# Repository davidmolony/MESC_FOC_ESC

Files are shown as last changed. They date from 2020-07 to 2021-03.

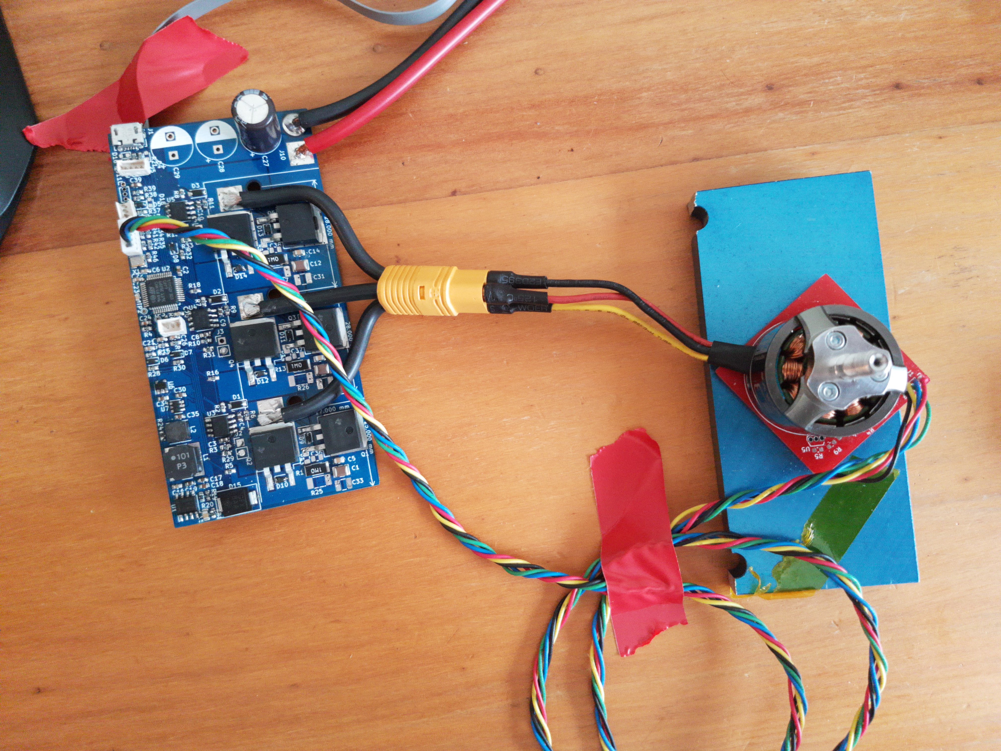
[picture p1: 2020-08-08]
MESC First Build and Propdrive 2826-1200kV.jpg

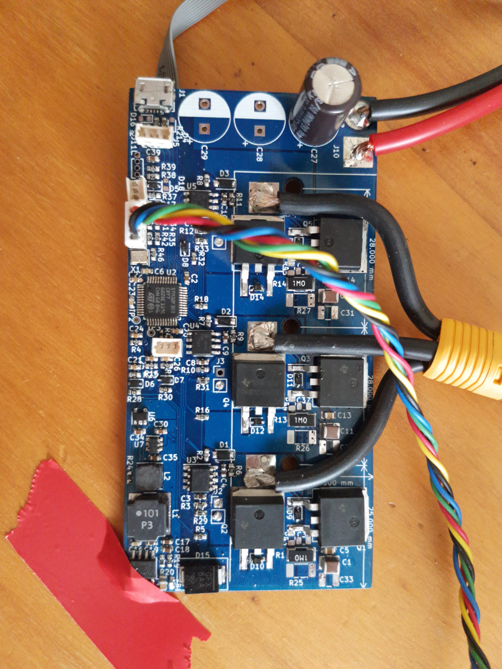
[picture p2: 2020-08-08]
MESC First build.jpg

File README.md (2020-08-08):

# MESC_FOC_ESC
MESC, Molony ESC, STM32F303 based FOC+BLDC ready, HALL, Encoder, Sensorless, single sides, 2 layer, ~90A @48V

This ESC is intended as a cost optimised alternative to the VESC, by utilising:

Standalone, industry standard footprint gate drivers

Standard D2PAK or H2PAK FETs

Cheap (~2.5$) STM32F303CB microcontroller

Board dimensions 100mmx50mm, so that it can be panelised and manufactured by JLCPCB, or two boards can be combined into one 100mm2 JLCPCB

It is not cross compatible with VESC software, and does not intend to be. VESC has run away with itself in terms of cost, firmware abstraction... in the opinion of this project's author.

# Current Status:  
First build has been made. All functions... function.
Photos in folder! Video of prelim run to be added to Youtube.
Step down works
Step up for Gate drives works
Chip works, all inputs and outputs works
Some concerns about stability of internal opamps... Returning 1.5V instead of 1.6V. First chip soldered returned 1V, and fluctuated by +0.3/-0.1V. 
Motor spins in BLDC mode (6 step) with hall sensors, on Propdrive 2826 1200kV and with APS8072 50kV. Current run up to 20A phase, with minimal PCB heating with no heatsink. Only run to 23V so far, owing to PSU limitation.
FET switching time rather slow with 5 ohm resistors, limiting peak current to 2A (not counting FET and Gate drive resistance) will reduce to 2R7.

# Layout:  
Layout optimised to minimise current loop path, and keep the board completely single sided assembly.

For thermal management, the FETs have vias underneath the drains, which can be interfaced with a heatsink on the PCB underside, using silicone pad/thermal paste & insulator.

# MCU uses:
Timer1 on PA8,9,10 (high) and PB13,14,15 for PWM generation.

Onboard opamps for current sensing and paralelled comparators input on pins PA1,7, PB0.

Phase voltages can be measured on PA3,4,5, or alternatively, digitally read to detect ZC .

Main voltage can be read on PA0.

# Interfaces:
External Interfaces include Hall/Encoder, I2C, PWM in, UART, USB FS.

Hall sensors on Timer4 PB6,7,8, alternatively Encoder can be run on Tim4 PB6,7

Timer3 channel 1 for standard RC PWM input.

USART3 Tx Rx on PB10,11.
USB on PA11,12, with 1k5 pullup to signal FS mode. Canbe used for reflashing (hypothetically).

I2C1 on PA15(SCL) and PB9(SDA), with a plug for a standard SSD1306 breakout. Alternatively, inertial sensor board could be plugged on breakout wire.

Expected BoM cost:  
0.4USD board  
6x2USD FETs  
2.5USD MCU  
3x1USD gate drives  
1USD SMPS converter  
0.4USD inductor  
??? connector cost (dependent on what's fitted, wire in...)  
0.3USD linear reg  
~3USD caps (dependent on how many you want to solder on, which is dependent on distance to battery, desire to comply with EMC, headroom above FET voltage... etc.)  
0.6USD shunts and other resistors  
0.3USD Optional TVS diode, primarily to protect SMPS, which is only rated to 65V  
Total: ~23-24USD

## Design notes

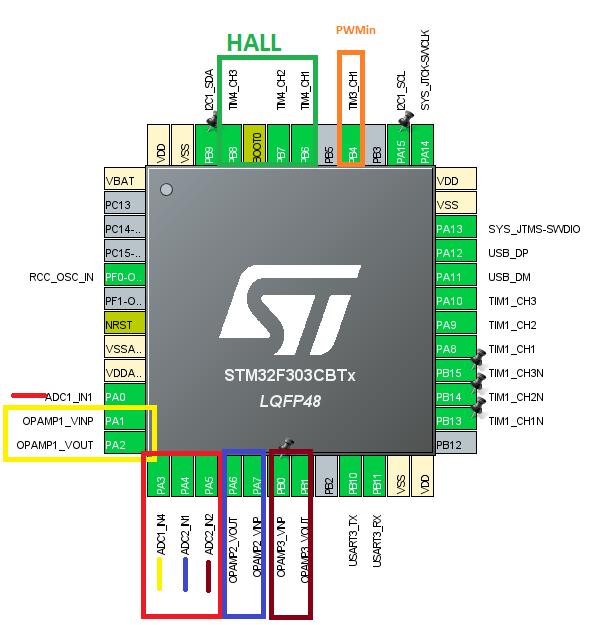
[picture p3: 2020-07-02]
CubeMX Pinout Annotated.JPG

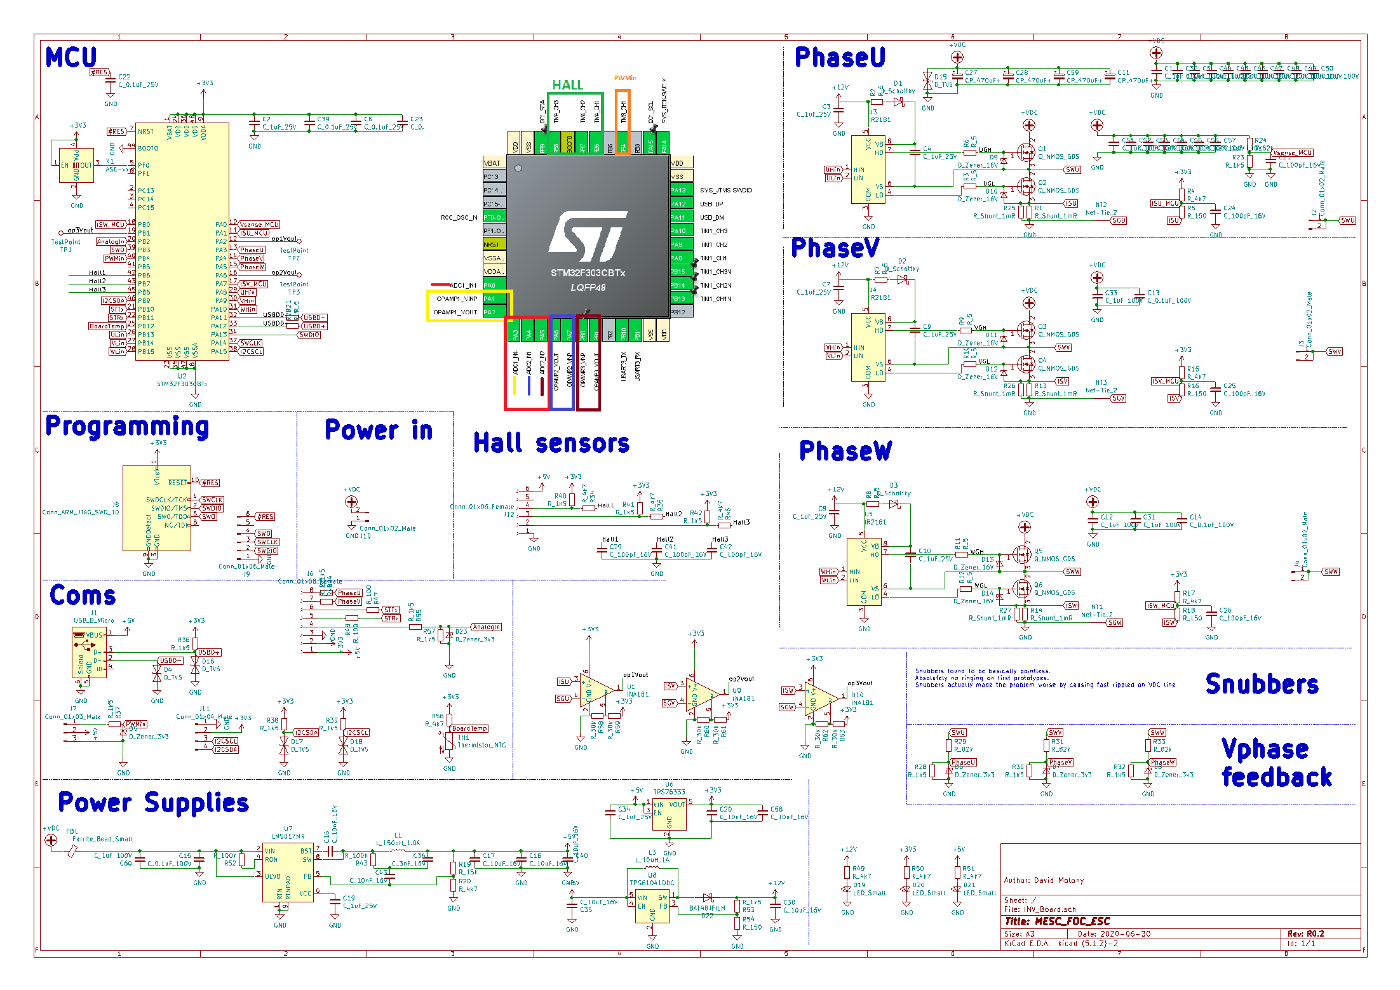
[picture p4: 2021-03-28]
Schematic MESC_FOC.png

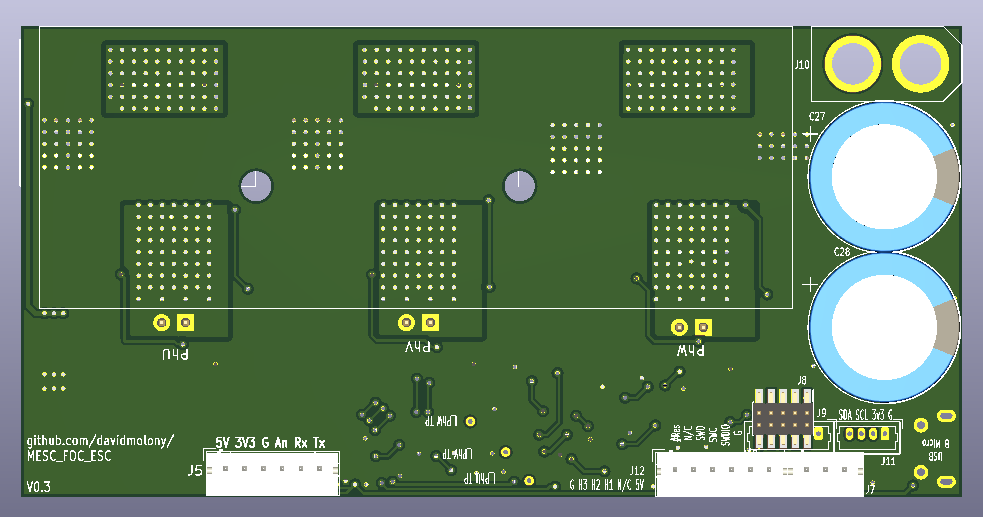
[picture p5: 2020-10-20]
MESC_FOC_ESC_Bottom_View.png

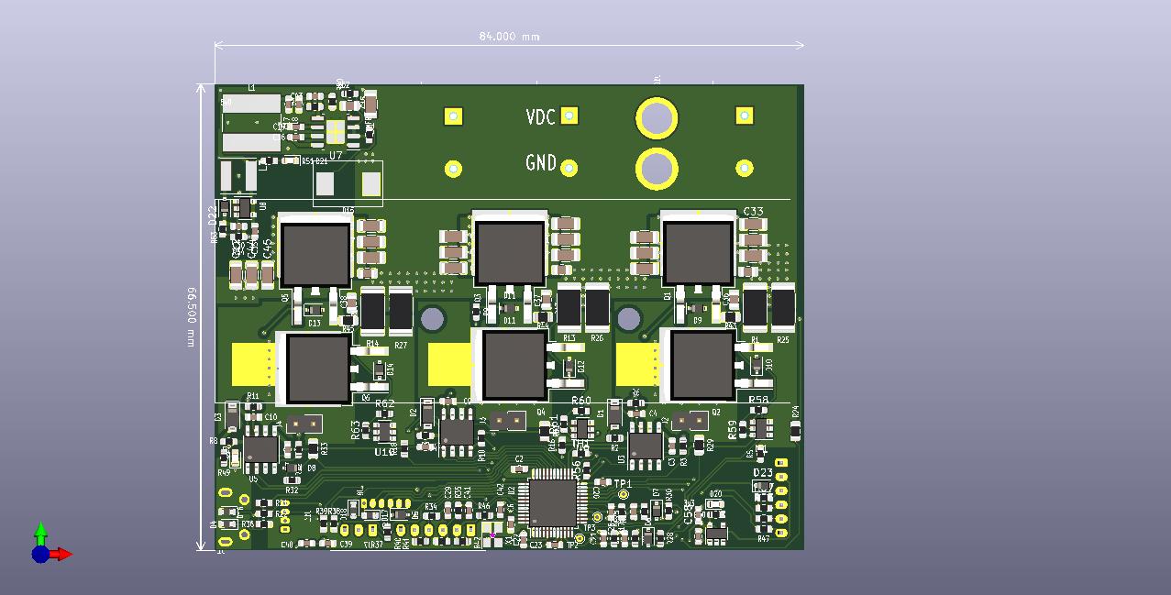
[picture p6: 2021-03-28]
V0.4 board top.jpg

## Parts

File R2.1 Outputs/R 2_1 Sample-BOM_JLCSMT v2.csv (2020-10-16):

Comment | Designator | Footprint | LCSC Part #(optional)
10uF 16V | C17,C18,C20,C30,C40 | 0603_C | C19702
1uF 25V | C2,C3,C4,C7,C8,C9,C10,C16,C19,C34 | 0603_C | C15849
100pF 16V | C21,C24,C25,C26,C29,C41,C42 | 0603_C | C14858
0.1uF 25V | C6,C22,C23,C35,C39 | 0603_C | C14663
0.01uF 100V | C36,C37,C38 | 0805_C | C22423
Zener 16V | D9,D10,D11,D12,D13,D14 | SOD-323_D | C150089
0603 LED | D19,D20,D21 | 0603_D | C2286
Schottky diode | D22 | SOD-323F_D | C2128
Schottky | D1,D2,D3 | SOD-123FL_D | C64898
Zener_3v3 | D5,D6,D7,D8 | SOD-323_D | C145245
MOSFET | Q1,Q2,Q3,Q4,Q5,Q6 | TO263-2_Q | C410926
150? | R5,R16,R18,R54 | 0603_R | C22808
15k? | R19 | 0603_R | C22809
4k7? | R4,R15,R17,R20,R34,R35,R46,R49,R50,R51 | 0603_R | C23162
5? | R2,R3,R6,R7,R8,R9,R10,R11,R12,R21,R22 | 0603_R | C23164
82k? | R24,R29,R31,R33 | 0805_R | C17840
2M? | R1,R13,R14,R25,R26,R27 | 2512_R | C60923
1k5? | R23,R28,R30,R32,R36,R37,R38,R39,R40,R41,R42,R53 | 0603_R | C22843
1? | R43,R44,R45 | 0805_R | C25271
100? | R47,R48 | 0603_R | C22775
30k? | R52 | 0603_R | C22984
STM32F303CB | U2 | LQFP-48_7.0x7.0x0.5P | C108516
TPS76333 | U6 | SOT-323-5_U | C110463
TPS61041DDC | U8 | SOT-323-5_U | C7722
OSCILLATORS 8MHz | X1 | SMD-OSC-3225_4P | C70556

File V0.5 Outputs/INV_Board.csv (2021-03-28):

Comment | Designator | Footprint | LCSC
C_1uF 100V | C1,C12,C31,C32,C33,C44,C45,C46,C47,C48,C49,C50,C51,C52,C53,C54,C55,C56,C57,C60 | Capacitor_SMD:C_1206_3216Metric | C13832
C_10nF_16V | C16,C43 | Capacitor_SMD:C_0603_1608Metric | C57112
C_10uF_16V | C17,C18,C20,C30,C35,C40,C58 | Capacitor_SMD:C_0603_1608Metric | C19702
C_1uF_25V | C2,C3,C4,C7,C8,C9,C10,C19,C34 | Capacitor_SMD:C_0603_1608Metric | C15849
C_100pF_16V | C21,C24,C25,C26,C29,C41,C42 | Capacitor_SMD:C_0603_1608Metric | C14858
C_0.1uF_25V | C6,C22,C23,C39 | Capacitor_SMD:C_0603_1608Metric | C14663
CP_470uF+ | C11,C27,C28,C59 | Capacitor_THT:CP_Radial_D16.0mm_P7.50mm
C_3nF_16V | C36 | Capacitor_SMD:C_0603_1608Metric | C1613
C_0.1uF_100V | C5,C13,C14,C15 | Capacitor_SMD:C_0805_2012Metric | C28233
D_Zener_16V | D9,D10,D11,D12,D13,D14 | Diode_SMD:D_SOD-323 | C150089
D_TVS | D15 | INV_Board:DO-214AB
D_TVS | D4,D16,D17,D18 | Diode_SMD:D_0603_1608Metric
LED_Small | D19,D20,D21 | LED_SMD:LED_0603_1608Metric | C2286
BAT48JFILM | D22 | Diode_SMD:D_SOD-323 | C2128
D_Schottky | D1,D2,D3 | Diode_SMD:D_SOD-123 | C64898
D_Zener_3v3 | D5,D6,D7,D8,D23 | Diode_SMD:D_SOD-323 | C145245
Ferrite_Bead_Small | FB1 | Resistor_SMD:R_0603_1608Metric | BLM18KG121TN1D
USB_B_Micro | J1 | Connector_USB:USB_Micro-B_Molex-105017-0001
Conn_01x02_Male | J10 | INV_Board:XT60
Conn_01x04_Male | J11 | Connector_Molex:Molex_PicoBlade_53047-0410_1x04_P1.25mm_Vertical
Conn_01x06_Female | J12 | Connector_JST:JST_PH_B6B-PH-K_1x06_P2.00mm_Vertical
Conn_01x02_Male | J2,J3,J4 | Connector_Wire:SolderWirePad_1x02_P5.08mm_Drill1.5mm
Conn_01x08_Female | J6 | Connector_JST:JST_PH_B8B-PH-K_1x08_P2.00mm_Vertical
Conn_01x03_Male | J7 | Connector_JST:JST_PH_B3B-PH-K_1x03_P2.00mm_Vertical
Conn_ARM_JTAG_SWD_10 | J8 | Connector_PinHeader_1.27mm:PinHeader_2x05_P1.27mm_Vertical_SMD
Conn_01x06_Male | J9 | Connector_Molex:Molex_PicoBlade_53047-0610_1x06_P1.25mm_Vertical
L_150uH_1.0A | L1 | Inductor_SMD:L_Bourns-SRN8040_8x8.15mm | C340248
L_10uH_1A | L3 | Inductor_SMD:L_Taiyo-Yuden_NR-50xx | C408339
Net-Tie_2 | NT1,NT2,NT3 | NetTie:NetTie-2_SMD_Pad0.5mm
Q_NMOS_GDS | Q1,Q2,Q3,Q4,Q5,Q6 | Package_TO_SOT_SMD:TO-263-2 | C455308
IPT015N10N5 | Q7,Q8,Q9,Q10,Q11,Q12 | Package_TO_SOT_SMD:Infineon_PG-HSOF-8-1 | C108964
R_150 | R5,R16,R18,R54 | Resistor_SMD:R_0603_1608Metric | C22808
R_15k | R19 | Resistor_SMD:R_0603_1608Metric | C22809
R_4k7 | R4,R15,R17,R20,R34,R35,R46,R49,R50,R51,R56 | Resistor_SMD:R_0603_1608Metric | C23162
R_5 | R2,R3,R6,R7,R8,R9,R10,R11,R12,R21,R22 | Resistor_SMD:R_0603_1608Metric | C23164
R_82k | R24,R29,R31,R33 | Resistor_SMD:R_0805_2012Metric | C17840
R_Shunt_1mR | R1,R13,R14,R25,R26,R27 | Resistor_SMD:R_2512_6332Metric | C270947
R_1k5 | R23,R28,R30,R32,R36,R37,R38,R39,R40,R41,R42,R44,R45,R53,R55,R57 | Resistor_SMD:R_0603_1608Metric | C22843
R_100 | R47,R48 | Resistor_SMD:R_0603_1608Metric | C22775
R_100k | R43,R52 | Resistor_SMD:R_0603_1608Metric | C25803
R_30k | R58,R59,R60,R61,R62,R63 | Resistor_SMD:R_0603_1608Metric | C22984
Thermistor_NTC | TH1 | Resistor_SMD:R_0603_1608Metric | C92367
TestPoint | TP1,TP2,TP3 | TestPoint:TestPoint_THTPad_D1.0mm_Drill0.5mm
INA181 | U1,U9,U10 | Package_TO_SOT_SMD:SOT-23-6
STM32F303CBTx | U2 | Package_QFP:LQFP-48_7x7mm_P0.5mm | C108516
IR2181 | U3,U4,U5 | Package_SO:SOIC-8_3.9x4.9mm_P1.27mm | C380794
TPS76333 | U6 | Package_TO_SOT_SMD:SOT-23-5 | C150720
LM5017MR | U7 | Package_SO:SOIC-8-1EP_3.9x4.9mm_P1.27mm_EP2.95x4.9mm_Mask2.71x3.4mm_ThermalVias | C34355
TPS61041DDC | U8 | Package_TO_SOT_SMD:SOT-23-5 | C7722
ASE-xxxMHz | X1 | Oscillator:Oscillator_SMD_Abracon_ASE-4Pin_3.2x2.5mm | C70556

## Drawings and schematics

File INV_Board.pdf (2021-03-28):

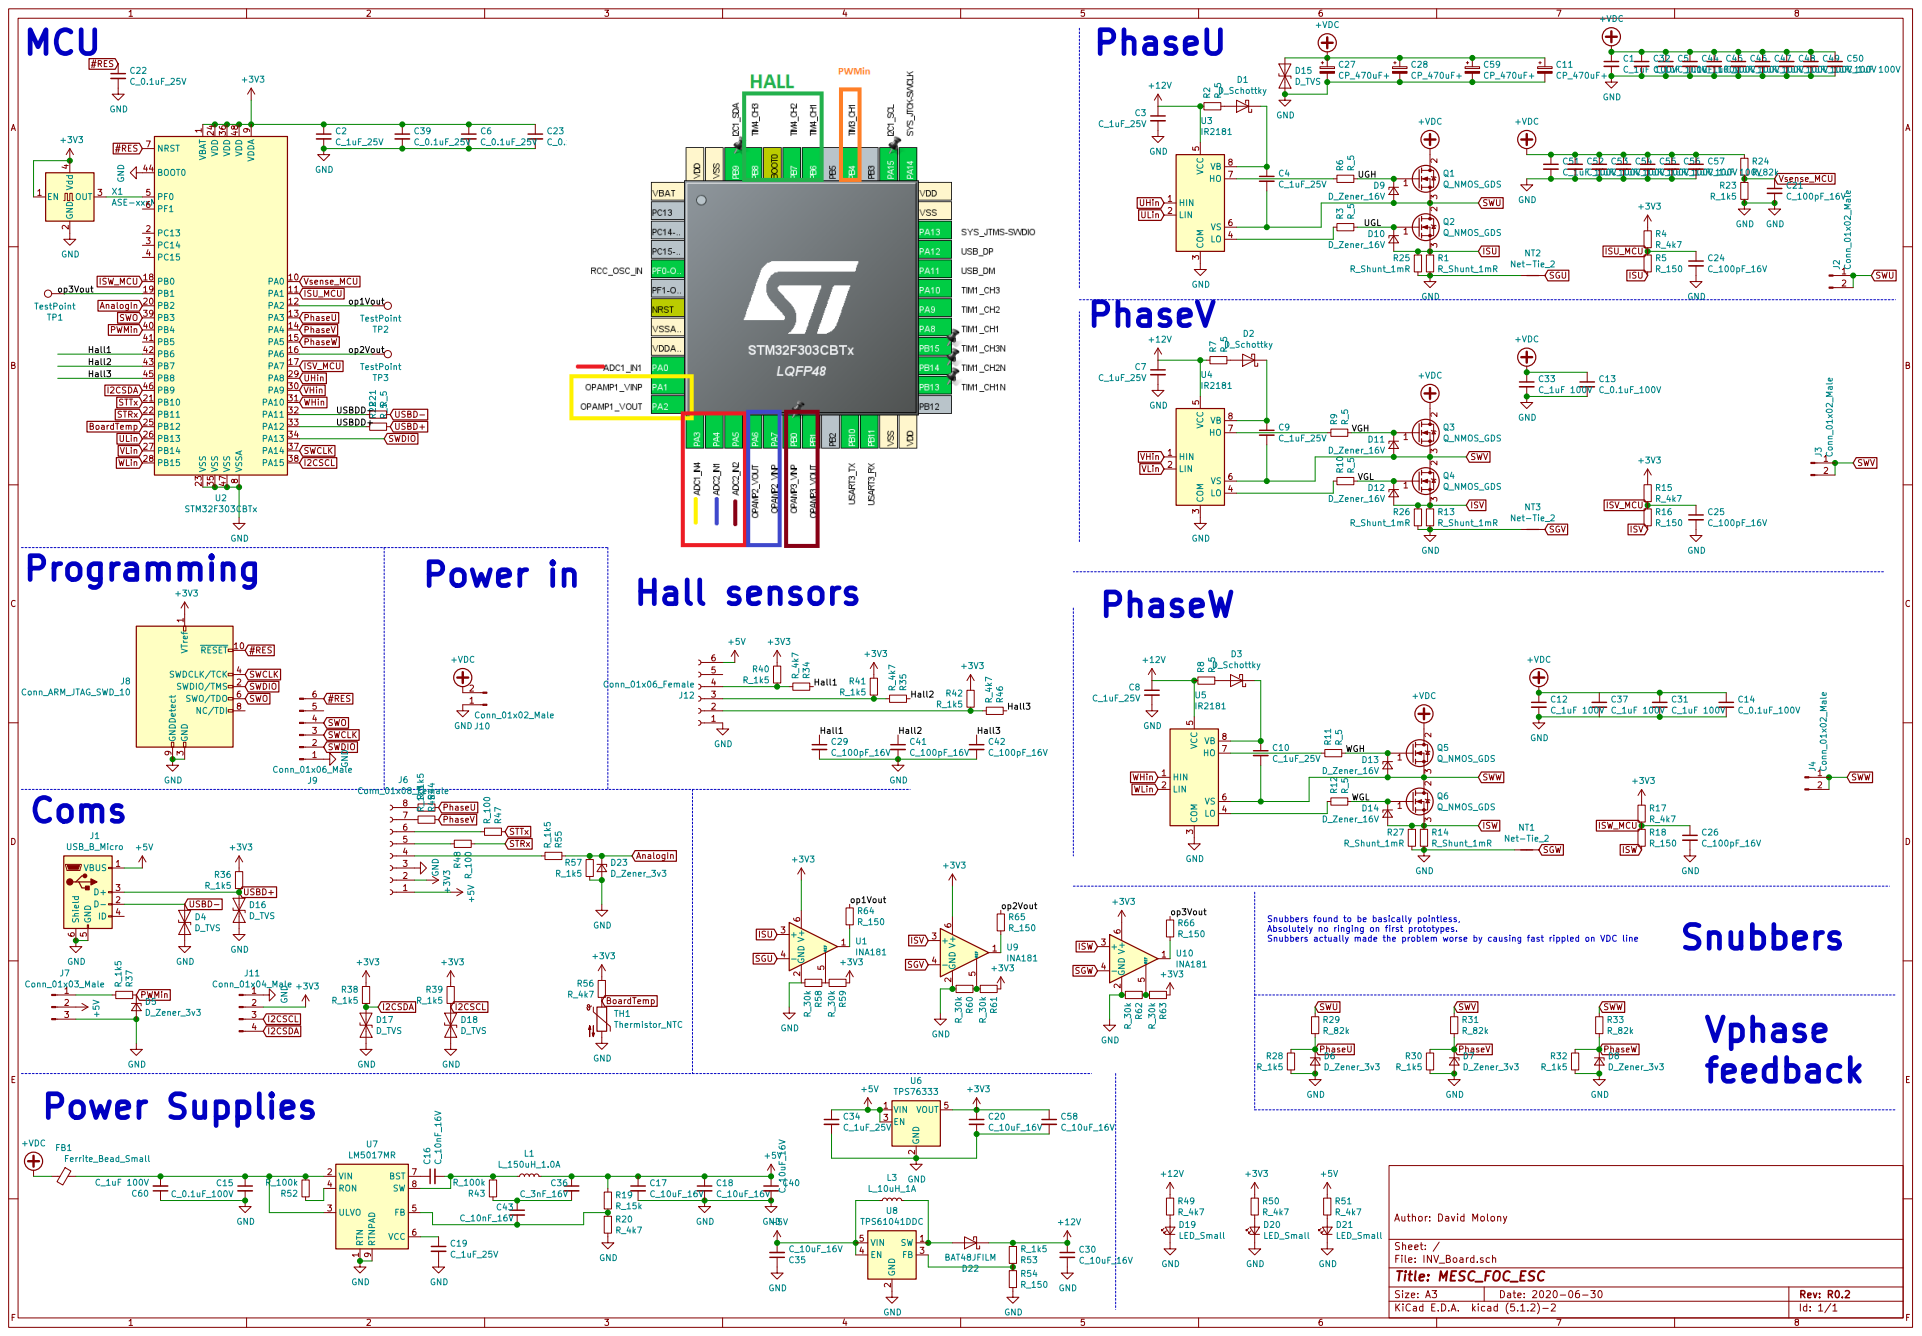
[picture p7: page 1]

1 VDD 24 VDD 36 VDD 48 VDDA
ISU_MCU GND

9 VSS 23 VSS 35 VSS 47 VSSA

VGL WGH WGL WGH WGL Snubbers found to be basically pointless,

3 SWDCLK/TCK 4 SWO/TDO 6 NC/TDI 8 GNDDetect 9

Absolutely no ringing on first prototypes.
Snubbers actually made the problem worse by causing fast rippled on VDC line

1 VIN 2 ULVO 3 RON 4 FB 5 VCC 6 BST 7 SW 8 RTNPAD

File: INV_Board.sch Sheet: / Author: David Molony

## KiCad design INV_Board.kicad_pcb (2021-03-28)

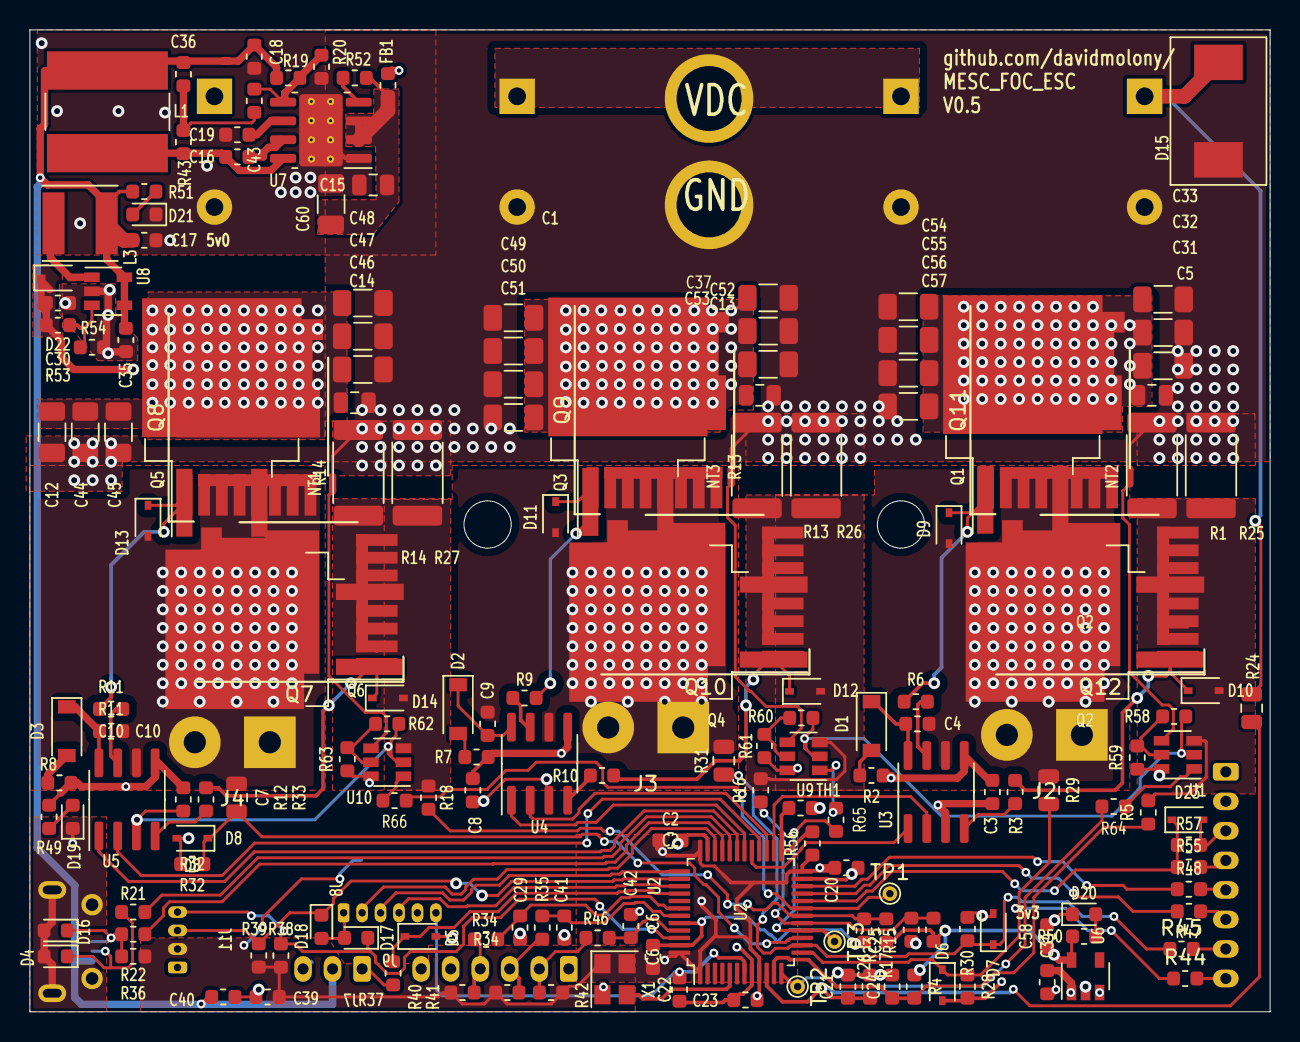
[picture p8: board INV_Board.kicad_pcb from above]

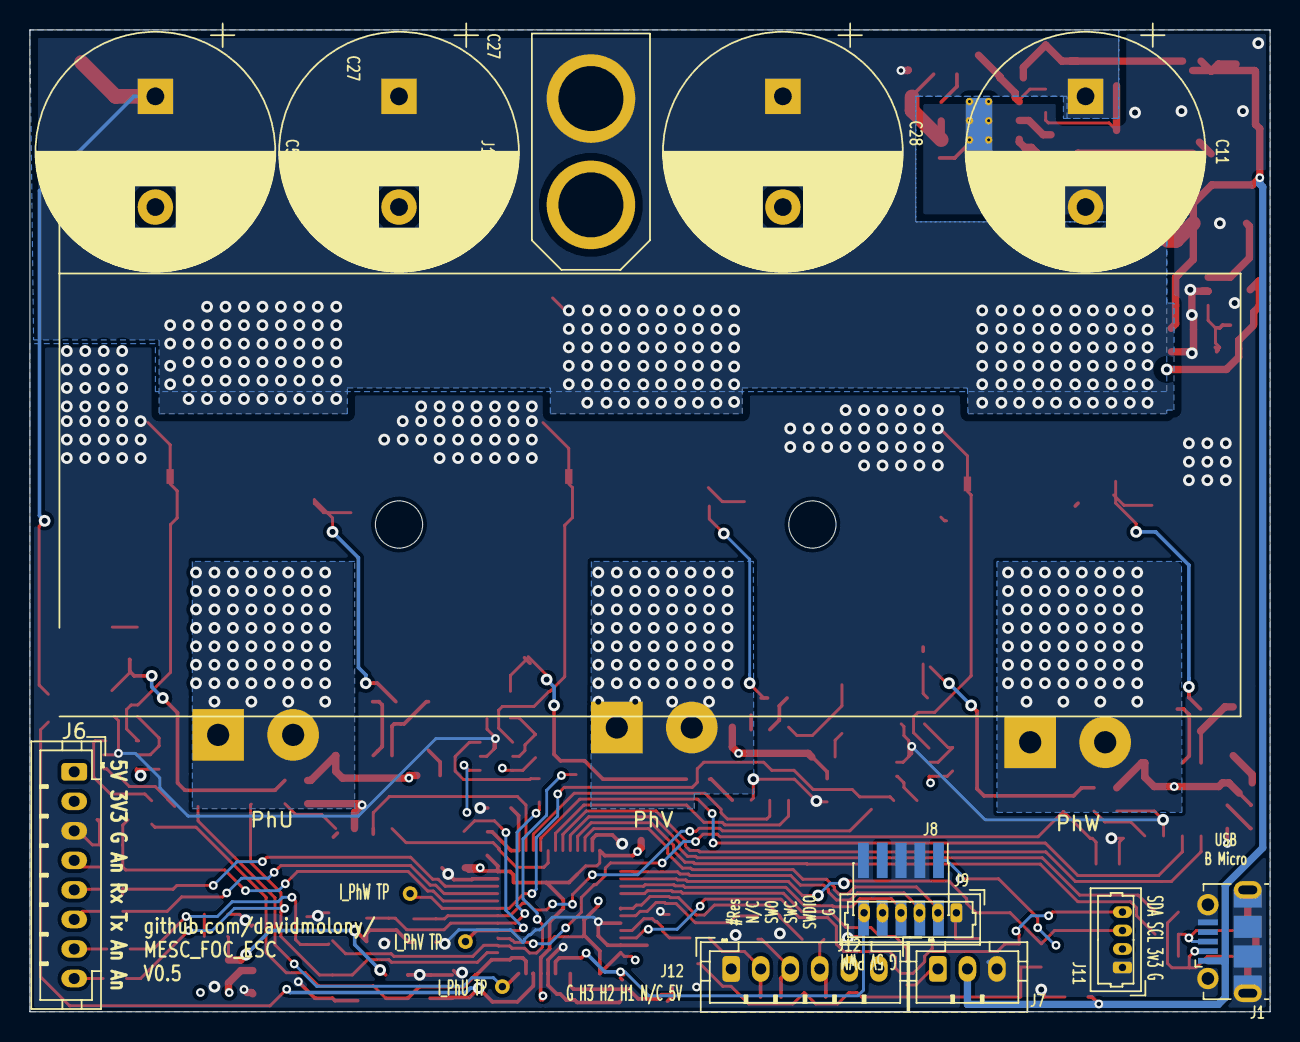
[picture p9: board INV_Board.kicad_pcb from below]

Board: 4 copper layers, 84.0 x 66.5 mm, 192 parts (12 on the bottom side), 94 nets.

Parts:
C1, C12, C31, C32, C33, C37, C44, C45, C46, C47, C48, C49, C50, C51, C52, C53, C54, C55, C56, C57, C60: C_1uF 100V; C_1206_3216Metric
C2, C3, C4, C7, C8, C9, C10, C19, C34: C_1uF_25V; C_0603_1608Metric
C5, C13, C14, C15: C_0.1uF_100V; C_0805_2012Metric
C6, C22, C23, C39: C_0.1uF_25V; C_0603_1608Metric
C11, C27, C28, C59: CP_470uF+; CP_Radial_D16.0mm_P7.50mm
C16, C43: C_10nF_16V; C_0603_1608Metric
C17, C18, C20, C30, C35, C40, C58: C_10uF_16V; C_0603_1608Metric
C21, C24, C25, C26, C29, C41, C42: C_100pF_16V; C_0603_1608Metric
C36: C_3nF_16V; C_0603_1608Metric
D1, D2, D3: D_Schottky; D_SOD-123
D4, D16, D17, D18: D_TVS; D_0603_1608Metric
D5, D6, D7, D8, D23: D_Zener_3v3; D_SOD-323
D9, D10, D11, D12, D13, D14: D_Zener_16V; D_SOD-323
D15: D_TVS; DO-214AB
D19, D20, D21: LED_Small; LED_0603_1608Metric
D22: BAT48JFILM; D_SOD-323
FB1: Ferrite_Bead_Small; R_0603_1608Metric
J1: USB_B_Micro; USB_Micro-B_Molex-105017-0001
J2, J3, J4: Conn_01x02_Male; SolderWirePad_1x02_P5.08mm_Drill1.5mm
J6: Conn_01x08_Female; JST_PH_B8B-PH-K_1x08_P2.00mm_Vertical
J7: Conn_01x03_Male; JST_PH_B3B-PH-K_1x03_P2.00mm_Vertical
J8: Conn_ARM_JTAG_SWD_10; PinHeader_2x05_P1.27mm_Vertical_SMD
J9: Conn_01x06_Male; Molex_PicoBlade_53047-0610_1x06_P1.25mm_Vertical
J10: Conn_01x02_Male; XT60
J11: Conn_01x04_Male; Molex_PicoBlade_53047-0410_1x04_P1.25mm_Vertical
J12: Conn_01x06_Female; JST_PH_B6B-PH-K_1x06_P2.00mm_Vertical
L1: L_150uH_1.0A; L_Bourns-SRN8040_8x8.15mm
L3: L_10uH_1A; L_Taiyo-Yuden_NR-50xx
NT1, NT2, NT3: Net-Tie_2; NetTie-2_SMD_Pad0.5mm
Q1, Q2, Q3, Q4, Q5, Q6: Q_NMOS_GDS; TO-263-2
Q7, Q8, Q9, Q10, Q11, Q12: IPT015N10N5; Infineon_PG-HSOF-8-1
R1, R13, R14, R25, R26, R27: R_Shunt_1mR; R_2512_6332Metric
R2, R3, R6, R7, R8, R9, R10, R11, R12, R21, R22: R_5; R_0603_1608Metric
R4, R15, R17, R20, R34, R35, R46, R49, R50, R51, R56: R_4k7; R_0603_1608Metric
R5, R16, R18, R54, R64, R65, R66: R_150; R_0603_1608Metric
R19: R_15k; R_0603_1608Metric
R23, R28, R30, R32, R36, R37, R38, R39, R40, R41, R42, R44, R45, R53, R55, R57: R_1k5; R_0603_1608Metric
R24, R29, R31, R33: R_82k; R_0805_2012Metric
R43, R52: R_100k; R_0603_1608Metric
R47, R48: R_100; R_0603_1608Metric
R58, R59, R60, R61, R62, R63: R_30k; R_0603_1608Metric
TH1: Thermistor_NTC; R_0603_1608Metric
TP1, TP2, TP3: TestPoint; TestPoint_THTPad_D1.0mm_Drill0.5mm
U1, U9, U10: INA181; SOT-23-6
U2: STM32F303CBTx; LQFP-48_7x7mm_P0.5mm
U3, U4, U5: IR2181; SOIC-8_3.9x4.9mm_P1.27mm
U6: TPS76333; SOT-23-5
U7: LM5017MR; SOIC-8-1EP_3.9x4.9mm_P1.27mm_EP2.95x4.9mm_Mask2.71x3.4mm_Th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
U8: TPS61041DDC; SOT-23-5
X1: ASE-xxxMHz; Oscillator_SMD_Abracon_ASE-4Pin_3.2x2.5mm

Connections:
#RES: C22.1, J8.10, J9.6, U2.7
+3V3: C2.1, C6.1, C20.1, C23.1, C39.1, C58.1, J6.2, J8.1, J11.2, R4.1, R15.1, R17.1, R36.1, R38.1, R39.1, R40.1, R41.1, R42.1, R50.1, R56.1, R59.1, R61.1, R63.1, U1.6, U2.1, U2.9, U2.24, U2.36, U2.48, U6.5, U9.6, U10.6, X1.1, X1.4
+5V: C17.1, C18.1, C34.1, C35.2, C36.1, C40.1, J1.1, J6.1, J7.2, J12.6, L1.2, L3.1, R19.1, R51.1, U6.1, U6.3, U8.4, U8.5
+12V: C3.1, C7.1, C8.1, C30.1, D22.1, R2.1, R7.1, R8.1, R49.1, R53.2, U3.5, U4.5, U5.5
+VDC: C1.1, C5.1, C11.1, C12.1, C13.1, C14.1, C27.1, C28.1, C31.1, C32.1, C33.1, C37.1, C44.1, C45.1, C46.1, C47.1, C48.1, C49.1, C50.1, C51.1, C52.1, C53.1, C54.1, C55.1, C56.1, C57.1, C59.1, D15.1, FB1.2, J10.2, Q1.2, Q3.2, Q5.2, Q8.3, Q9.3, Q11.3, R24.1
/Hall1: C29.1, R34.1, U2.42
/Hall2: C41.1, R35.1, U2.43
/Hall3: C42.1, R46.1, U2.45
/UGH: D9.1, Q1.1, Q11.1, R6.2
/UGL: D10.1, Q2.1, Q12.1, R3.2
/USBDD+: R22.1, U2.33
/USBDD-: R21.1, U2.32
/VGH: D11.1, Q3.1, Q9.1, R9.2
/VGL: D12.1, Q4.1, Q10.1, R10.2
/WGH: D13.1, Q5.1, Q8.1, R11.2
/WGL: D14.1, Q6.1, Q7.1, R12.2
/op1Vout: R64.1, TP2.1, U2.12
/op2Vout: R65.1, TP3.1, U2.16
/op3Vout: R66.1, TP1.1, U2.19
AnalogIn: D23.1, R55.1, R57.1, U2.20
BoardTemp: R56.2, TH1.1, U2.25
GND: C1.2, C2.2, C3.2, C5.2, C6.2, C7.2, C8.2, C11.2, C12.2, C13.2, C14.2, C15.2, C17.2, C18.2, C19.2, C20.2, C21.2, C22.2, C23.2, C24.2, C25.2, C26.2, C27.2, C28.2, C29.2, C30.2, C31.2, C32.2, C33.2, C34.2, C35.1, C37.2, C39.2, C40.2, C41.2, C42.2, C44.2, C45.2, C46.2, C47.2, C48.2, C49.2, C50.2, C51.2, C52.2, C53.2, C54.2, C55.2, C56.2, C57.2, C58.2, C59.2, C60.1, D4.2, D5.2, D6.2, D7.2, D8.2, D15.2, D16.2, D17.2, D18.2, D19.1, D20.1, D21.1, D23.2, J1.5, J1.6, J6.3, J7.3, J8.3, J8.5, J8.9, J9.1, J10.1, J11.1, J12.1, NT1.2, NT2.2, NT3.2, R1.2, R13.2, R14.2, R20.2, R23.2, R25.2, R26.2, R27.2, R28.2, R30.2, R32.2, R54.2, R57.2, R58.2, R60.2, R62.2, TH1.2, U1.2, U2.8, U2.23, U2.35, U2.44, U2.47, U3.3, U4.3, U5.3, U6.2, U7.1, U7.9, U8.2, U9.2, U10.2, X1.2
I2CSCL: D18.1, J11.3, R39.2, U2.38
I2CSDA: D17.1, J11.4, R38.2, U2.46
ISU: D10.2, Q2.3, Q12.2, R1.1, R5.2, R25.1, U1.3
ISU_MCU: C24.1, R4.2, R5.1, U2.11
ISV: D12.2, Q4.3, Q10.2, R13.1, R16.2, R26.1, U9.3
ISV_MCU: C25.1, R15.2, R16.1, U2.17
ISW: D14.2, Q6.3, Q7.2, R14.1, R18.2, R27.1, U10.3
ISW_MCU: C26.1, R17.2, R18.1, U2.18
unnamed: C4.1, D1.1, U3.8
unnamed: C9.1, D2.1, U4.8
unnamed: C10.1, D3.1, U5.8
unnamed: C15.1, C60.2, FB1.1, R52.2, U7.2, U7.3
unnamed: C16.1, U7.7
unnamed: C16.2, L1.1, R43.2, U7.8
unnamed: C19.1, U7.6
unnamed: C36.2, C43.1, R43.1
unnamed: C43.2, R19.2, R20.1, U7.5
unnamed: D1.2, R2.2
unnamed: D2.2, R7.2
unnamed: D3.2, R8.2
unnamed: D19.2, R49.2
unnamed: D20.2, R50.2
unnamed: D21.2, R51.2
unnamed: D22.2, L3.2, U8.1
unnamed: J6.4, R55.2
unnamed: J6.5, R48.1
unnamed: J6.6, R47.2
unnamed: J6.7, R45.2
unnamed: J6.8, R44.2
unnamed: J7.1, R37.2
unnamed: J12.2, R42.2, R46.2
unnamed: J12.3, R35.2, R41.2
unnamed: J12.4, R34.2, R40.2
unnamed: R3.1, U3.4
unnamed: R6.1, U3.7
unnamed: R9.1, U4.7
unnamed: R10.1, U4.4
unnamed: R11.1, U5.7
unnamed: R12.1, U5.4
unnamed: R52.1, U7.4
unnamed: R53.1, R54.1, U8.3
unnamed: R58.1, R59.2, U1.5
unnamed: R60.1, R61.2, U9.5
unnamed: R62.1, R63.2, U10.5
unnamed: R64.2, U1.1
unnamed: R65.2, U9.1
unnamed: R66.2, U10.1
unnamed: U2.5, X1.3
PWMin: D5.1, R37.1, U2.40
PhaseU: D6.1, R28.1, R29.2, R44.1, U2.13
PhaseV: D7.1, R30.1, R31.2, R45.1, U2.14
PhaseW: D8.1, R32.1, R33.2, U2.15
SGU: NT2.1, U1.4
SGV: NT3.1, U9.4
SGW: NT1.1, U10.4
STRx: R48.2, U2.22
STTx: R47.1, U2.21
SWCLK: J8.4, J9.3, U2.37
SWDIO: J8.2, J9.2, U2.34
SWO: J8.6, J9.4, U2.39
SWU: C4.2, D9.2, J2.1, J2.2, Q1.3, Q2.2, Q11.2, Q12.3, R29.1, U3.6
SWV: C9.2, D11.2, J3.1, J3.2, Q3.3, Q4.2, Q9.2, Q10.3, R31.1, U4.6
SWW: C10.2, D13.2, J4.1, J4.2, Q5.3, Q6.2, Q7.3, Q8.2, R33.1, U5.6
UHin: U2.29, U3.1
ULin: U2.26, U3.2
USBD+: D16.1, J1.3, R22.2, R36.2
USBD-: D4.1, J1.2, R21.2
VHin: U2.30, U4.1
VLin: U2.27, U4.2
Vsense_MCU: C21.1, R23.1, R24.2, U2.10
WHin: U2.31, U5.1
WLin: U2.28, U5.2

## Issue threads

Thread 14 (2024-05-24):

How can I get MESC PCBA? How much is it? Thank you .

chrismolony, 2024-05-24:
How can I get MESC PCBA? How much is it? Thank you .

davidmolony, 2024-05-24:
The files should (might?) still work with jlcpcb, or you can check out the kicad and regenerate them. It's nearly 3 years since i ordered this and the firmware is now primarily developed on f405rg chips.

The hardware still performs surprisingly well, but there's probably better open source these days. It's mega cheap to produce though!

I paid iirc 150usd for 5x populated boards without capacitors 3 years ago. Can probably get it for similar price now if you use e.g hyg015n10 MOSFETs.

StevenShiChina, 2024-05-25:
Thanks for your reply. Could you provide the schematic diagram based on the F405rg?  I only found F303CB schematic diagram in your repository.  And what is your e-mail address? or how can I contact you quickly? facebook  or wechat ?

davidmolony, 2024-05-25:
https://github.com/badgineer/MP2-ESC with
https://github.com/davidmolony/F405_pill

This is the closest to a public f405rg device. Really, MESC became a firmware project supporting loads of different ST MCUs.
https://github.com/davidmolony/MESC_Firmware

Closed 2024-05-26.

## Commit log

2020-06-27 Initial design upload - Full PCB layout with all interfaces - candidate final design.
    [INV_Board.kicad_pcb, INV_Board.sch]
2020-06-27 Commit changes to put omitted Vias on TVS ground.
    [INV_Board.kicad_pcb]
2020-06-30 Updates to add extra ceramic caps on power line next to FETs, move high frequency 0805 capacitor to closest position next to FETs, move shunts in a fewmm to reduce inductive current loops, update sch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
    [INV_Board.kicad_pcb, INV_Board.sch]
2020-07-05 Update to add 5V rail using TPS560430, smaller 3v3 reg, 3v3 pullups and 5V power on hall sensors, tidy up the schematic a bit.
    [INV_Board.kicad_pcb, INV_Board.sch]
2020-07-09 Tidied up schematic, added snubber pads using 0805 cap and resistor as close as possible to FETs (courtyards infringed, but this is intentional to improve performance), added ferrite bead in front of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
    [INV_Board.kicad_pcb, INV_Board.sch]
2020-07-10 Change power scheme to have 5V rail genreated from LMR36510, and then boost it up to 12V for the gate drivers, which use very little power. This scheme allows the use of a seperate power source for t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
    [INV_Board-B_Cu.gbr, INV_Board-B_Mask.gbr, INV_Board-B_Paste.gbr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]
2020-07-11 Added input resistors on Hall lines, added TVS protection on input lines I2C, USB UART protected with 0402 resistors, since no space... ToDo... fit 0603 or learn to solder 0402... ugh.
    [INV_Board-B_Cu.gbr, INV_Board-B_Mask.gbr, INV_Board-B_Paste.gbr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]
2020-07-24 Update R values on power and switch lines to 1k5 and 47k 0805 to enable voltages up to 3.3*48.5/1.5=106V. Add power LEDs and extra 5V cap near USB. Change all text to 0.8mm to make it tidier.
    [INV_Board-B_Cu.gbr, INV_Board-B_Mask.gbr, INV_Board-B_Paste.gbr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]
2020-07-25 Added SWO line to the JTAG header to aid debugging and live variable tracking. Will have to manually mod with wire the first set of boards ordered.
    [INV_Board.kicad_pcb, INV_Board.sch]
2020-08-08 Add a licence, based on BSD 3 clause with mods to say HARDWARE DESIGN in addition to SOFTWARE, and stipulate that production of the design must have a silkscreen reference to manufacturer and the pro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
2020-09-02 Connectors now JST PH series for throttle and hall sensor input, routing for Iu improved, larger capacitors (2x) 6 pin header to include SWO connectivity, 0402 removed, extra capacitors on Hall senso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
    [INV_Board (2).csv, INV_Board (3).csv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]
2020-09-09 As ordered R2_2. Updated to use TPS61040 since JLCPCB have them as basic parts plus LM5163 capable, for 100V. XT60 PCB mount connectors, large 16mm diameter caps. 5 samples ordered with CRMicro FETs
    [INV_Board BoM R2_2.csv, INV_Board JLC Fit R2_1 v2.csv, INV_Board JLC Fit R2_1.CSV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]
2020-10-20 Moved PSU, Added analog in & converted UART to JST PH with VESC pinout, added TP for opamp3, added thermistor, added FAN73901 to the JLCPCB BoM, swapped to LM5017 DCDC, added inductors to BoM, added 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
    [INV_Board.kicad_pcb, INV_Board.sch]
2020-11-11 Massive redesign of board to have much bigger power paths (3x the copper and shorter returns) anda 66*84 aspect ratio instead of 50*100. Initial positions for INA181 chips put down.
    [INV_Board.kicad_pcb, INV_Board.sch]
2020-11-20 Provisional rearrangement of board to optimise the layout for power paths in light of Zombies comments, and addition of INA181 opamp options.
    [INV_Board.kicad_pcb, INV_Board.sch, Inductance resistance comparison.ods]
2020-12-16 As ordered from JLC PCB 15-12-20, external opamps, rerranged for low impedance ground and Vin and moved DCDC. Added optional input analog on phase voltage wires.
    [INV_Board-B_Cu.gbr, INV_Board-B_Mask.gbr, INV_Board-B_Paste.gbr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]
2021-01-16 Add series resistors to the opamp outputs, this will protect against fighting MCU and ops. Move the Ceramic caps near the DCDC to clear possible top fit capacitors. Increase clearance for different s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
    [INV_Board.kicad_pcb, INV_Board.sch]
2021-01-16 Optimise layout of DCDC boost to eliminate inducive loop on DCDC, hopefully eliminate ringing.
    [INV_Board.kicad_pcb]
2021-01-16 Images of burnt BMS FETs
2021-01-16 Pic of boards for Qwerkus and Stancecoke
2021-03-28 Generate PDF Schematic
